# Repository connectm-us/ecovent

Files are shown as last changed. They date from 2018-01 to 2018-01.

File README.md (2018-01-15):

# ecovent
Open source repository for Ecovent smart vent, hub, and wall sensor designs

## Purpose

To open the hardware to the public, open-source community in an effort to stimulate more effective and cost-efficient designs for hardware.

## Methodology

By leveraging a network of sensors measuring temperature, pressure, humidity in rooms throughout a building, and vents or dampers with temperature and pressure sensors, that can be remotely controlled to provide room by room climate control, we can focus on commoditizing the hardware to open this technology to the mass market.

## Room By Room Climate Control Method

A system including a controlled supply register that has an airflow adjusting mechanism that controls an aperture through which air passes and a register sensor that senses a value of an environmental variable in a systems duct work. The register also includes a communication system and a processor system that controls the airflow adjusting mechanism. The system also includes a sensor platform that senses an environmental variable in a space and transmits and receives information. The system includes a controller that receives information about the environmental variables and a desired set point for the environmental variable in the space, controlled via application. The controller determines a target airflow to achieve the desired set point and transmits information about the target airflow. The register receives information about the target airflow and controls the register adjusting mechanism to achieve the target airflow.

## Mass Market
If we can produce cost-efficient dampers or supply registers and sensors to operate within this system methodology, we can provide a solution to the mass market for less than $500.

## Proven Technology
We have proven this technology over 4 years, with independent studies and in-the-field systems.  We are title 24 compliant as well.  The methodology is proven.  Now we need to commoditize the hardware.

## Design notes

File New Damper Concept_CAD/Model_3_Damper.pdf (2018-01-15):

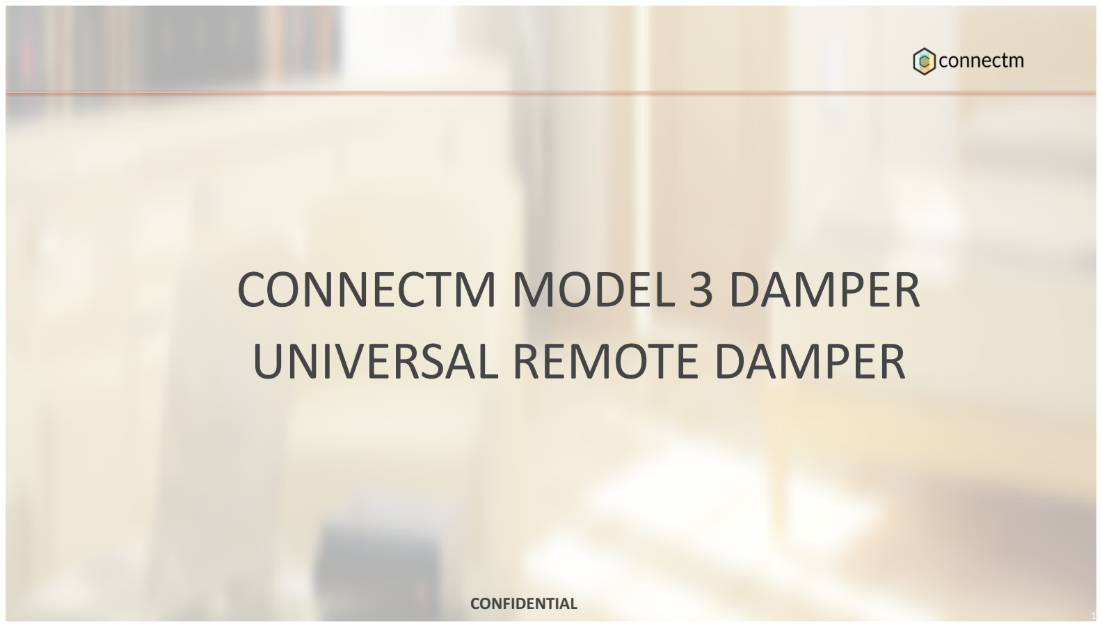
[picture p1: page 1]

# CONNECTM MODEL 3 DAMPER UNIVERSAL REMOTE DAMPER

1

### CONFIDENTIAL

Page 2

# Key Requirements

# - Interface with standard straight vent HVAC boot (4”, 6”, & 8” diameter)

## – Sheet metal construction – 4” diameter vent chosen for layout

# - Target Cost: ~$20 - Target volume: 500k-1M units per year - Operating Environment

## – Temperature: 0-85 C – Humidity: Standard HVAC

# - Target Flow Rate: 0-125 CFM - Target Pressure: 0”-2” H2O - Low Noise - Batteries:

## – 3-5 year life – User-accessible compartment

# - Duty Cycle: 10 full open/close cycles per day - Open / Close Speed: no specific requirement (slow speed OK)

CONFIDENTIAL

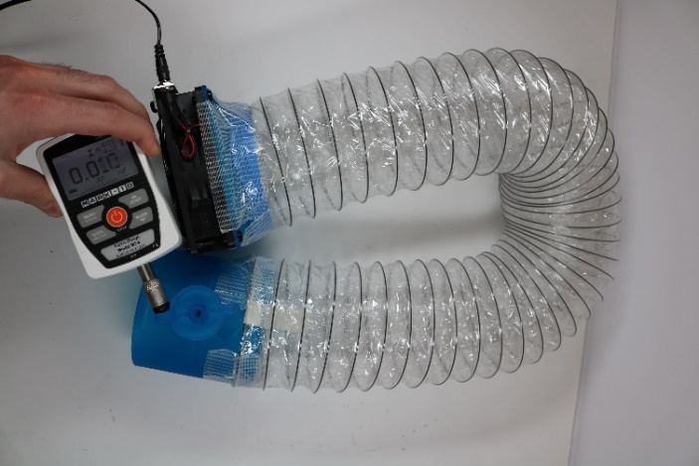
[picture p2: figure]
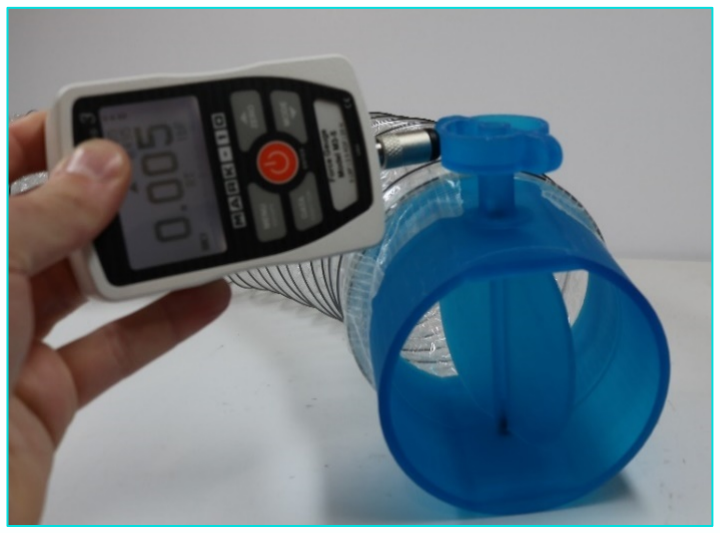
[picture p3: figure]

Page

3

# Motor Torque Requirement Testing

# - Motor sourcing exercise required evaluation of approximate expected open/close damper torque - Off the shelf 120 CFM fan operating at 0.4”

H20 used as airflow source.

# - Rapid prototype damper and housing printed

# - Torque range measured as follows: – Measured peak torque: 0.025 in-lbs (2.8

# mNm

)

# – 5x Safety Factor applied – Target motor torque: 0.120 in -lbs (13 mNm

)

CONFIDENTIAL

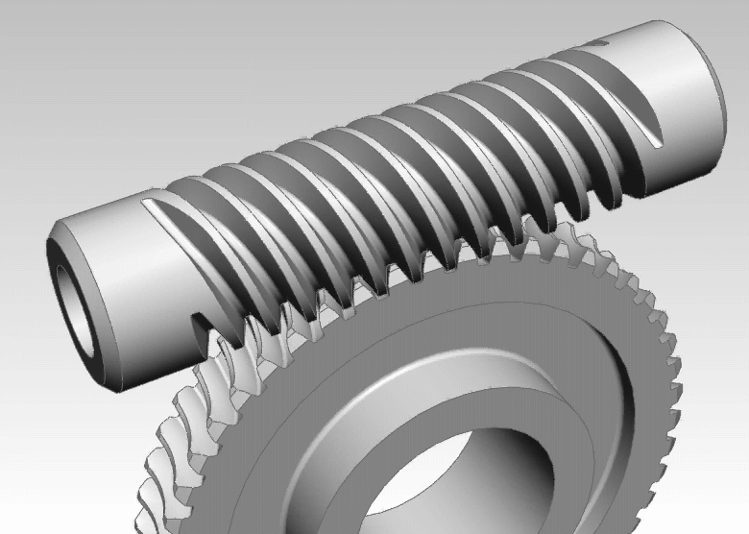
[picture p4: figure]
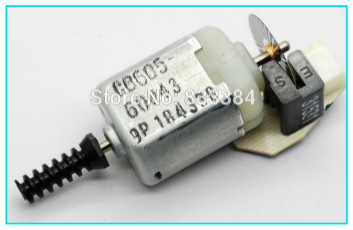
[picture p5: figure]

Page

4

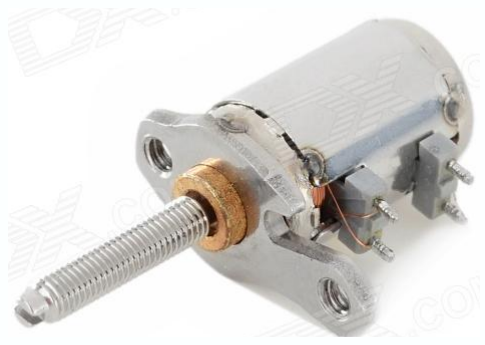
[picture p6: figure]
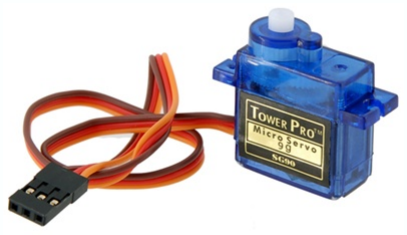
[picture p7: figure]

# 1.Drive Options:

# 1.DC Motor 2.Stepper Motor 3.Servo Motor

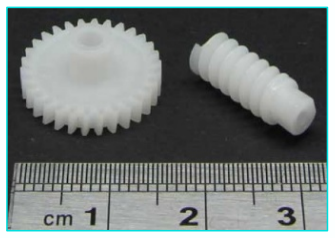
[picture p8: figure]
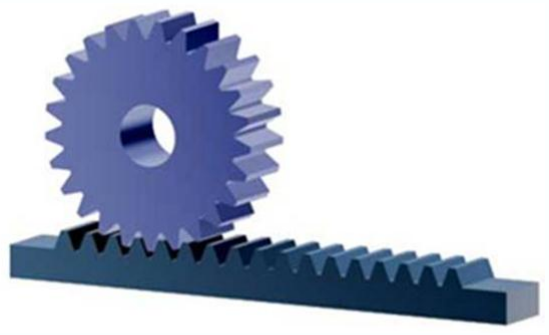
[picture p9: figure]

# 2.Drivetrain Options:

# 1.Worm Gear 2.Rack and Pinion

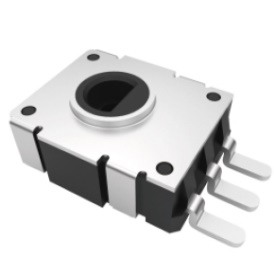
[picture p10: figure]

# 3.Belt Drive

# 3.Rotational Position Sensor

# 1.Stepper with zeroing / calibration 2.Potentiometer with lookup value 3.Encoder direct on motor

# Motor / Drivetrain / Position Options

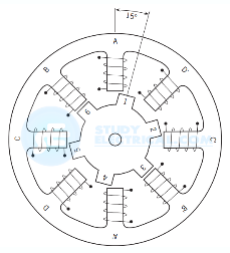
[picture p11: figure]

CONFIDENTIAL

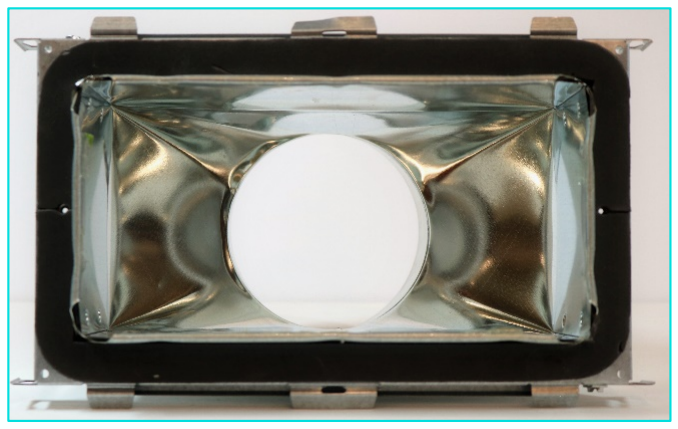
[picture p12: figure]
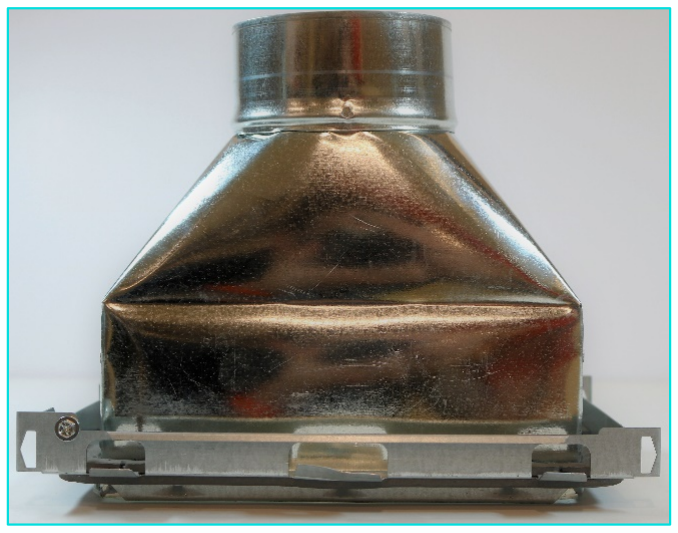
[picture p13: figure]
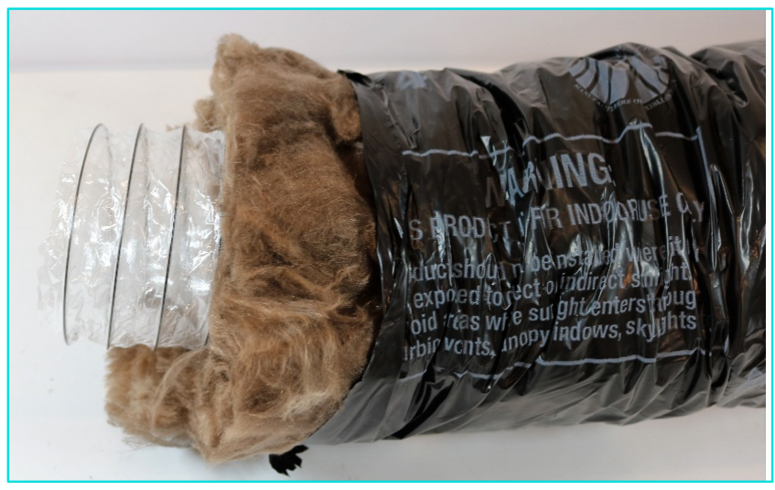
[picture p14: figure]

ConnectM Technology Solutions | Page 5

# HVAC Design Constraints

# - 4” x 8” HVAC straight vent boot - 4” Insulated flexible ducting

# CAD Layout Review

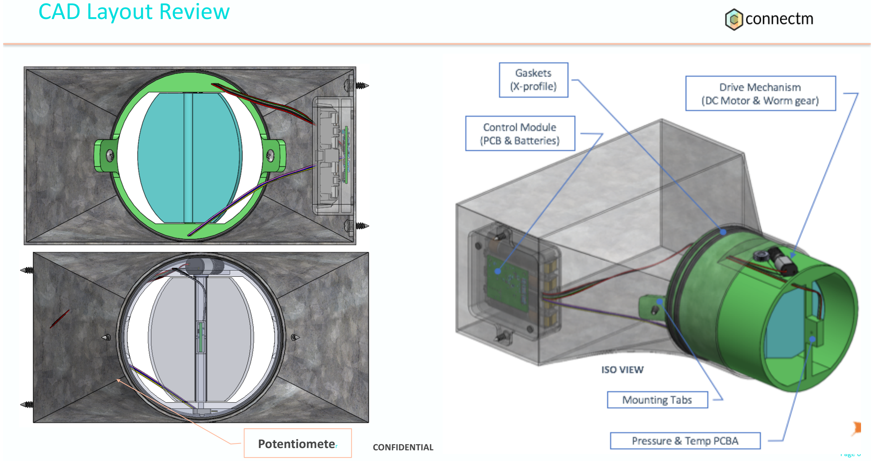
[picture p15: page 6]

CONFIDENTIAL
Page 6

### Potentiometer

Page 7

# Preliminary BOM Estimate

Level | Qty. | Component | Est. Cost (500k/yr) | Ext. Cost | Comments
0 | 1 | CONTROL MODULE ASSY | $ | 6.85 | $ | 6.85
1 | 1 | Control Module Housing, Bottom | $ | 1.00 | $ | 1.00 Estimated for plastic injection molding
1 | 1 | Control Module Housing, Cover | $ | 0.40 | $ | 0.40 | Estimated for plastic injection molding
1 | 2 | Closure Magnets | $ | 0.05 | $ | 0.10 Approximate Pricing from K&J Magnetics
1 | 2 | Double (-) AA Clip Contact | $ | 0.20 | $ | 0.40 | Approximate Pricing from Digi-Key (MPD Devices part)
1 | 2 | Double (+) AA Clip Contact | $ | 0.20 | $ | 0.40 Approximate Pricing from Digi-Key (MPD Devices part)
1 | 1 | PCB Control Assemby | $ | 5.00 | $ | 5.00 | Ecovent to confirm cost
1 | 4 | AA Battery | $ | 0.10 | $ | 0.40 Approximate Pricing from Digi-Key
0 | 1 | DAMPER ASSY | $ | 8.95 | $ | 9.30
1 | 1 | Pressure & Temp PCBA | $ | 3.00 | $ | 3.00 Ecovent to confirm cost
1 | 1 | Damper Housing | $ | 2.00 | $ | 2.00 | Estimated for plastic injection molding
1 | 1 | Damper Valve | $ | 0.50 | $ | 0.50 Estimated for plastic injection molding
1 | 1 | Worm Gear | $ | 0.25 | $ | 0.25 | Estimated for plastic injection molding
1 | 1 | Worm Drive | $ | 0.35 | $ | 0.35 Estimated for plastic injection molding
1 | 2 | O-Ring | $ | 0.35 | $ | 0.70 | Estimate for LSR injection molding
1 | 1 | DC Motor | $ | 2.50 | $ | 2.50 Based on discussions with Mabuchi and Nidec
1 | 1 | Potentiometer | $ | 0.10 | $ | 0.10 | Based on discussions with Polyshine
0 | 1 | MOTOR WIRE HARNESS | $ | 0.25 | $ | 0.25 Estimate
0 | 1 | MEASUREMENT WIRE HARNESS | $ | 0.50 | $ | 0.50 | Estimate
0 | 1 | POT WIRE HARNESS | $ | 0.25 | $ | 0.25 Estimate
0 | 1 | MANUAL ASSEMBLY | $ | 2.50 | $ | 2.50 | 10 min assy time estimate @ $15/hr
| | TOTAL BOM COST: | | | $ | 19.65
| | | | CONFIDENTIAL

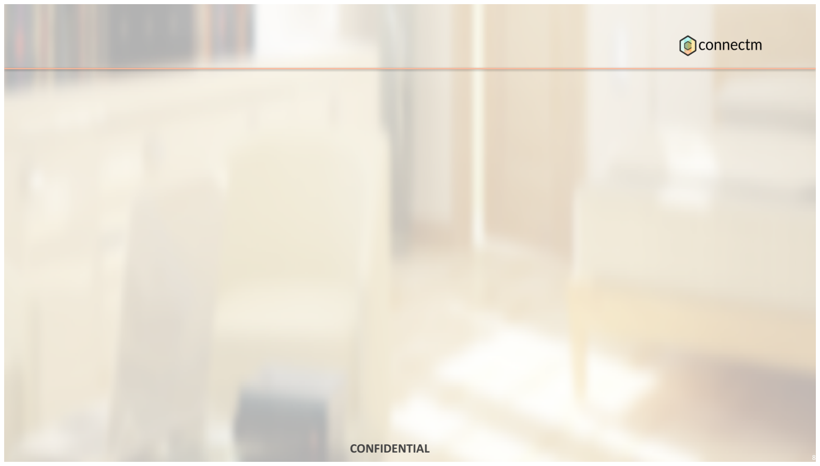
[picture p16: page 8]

8

### CONFIDENTIAL

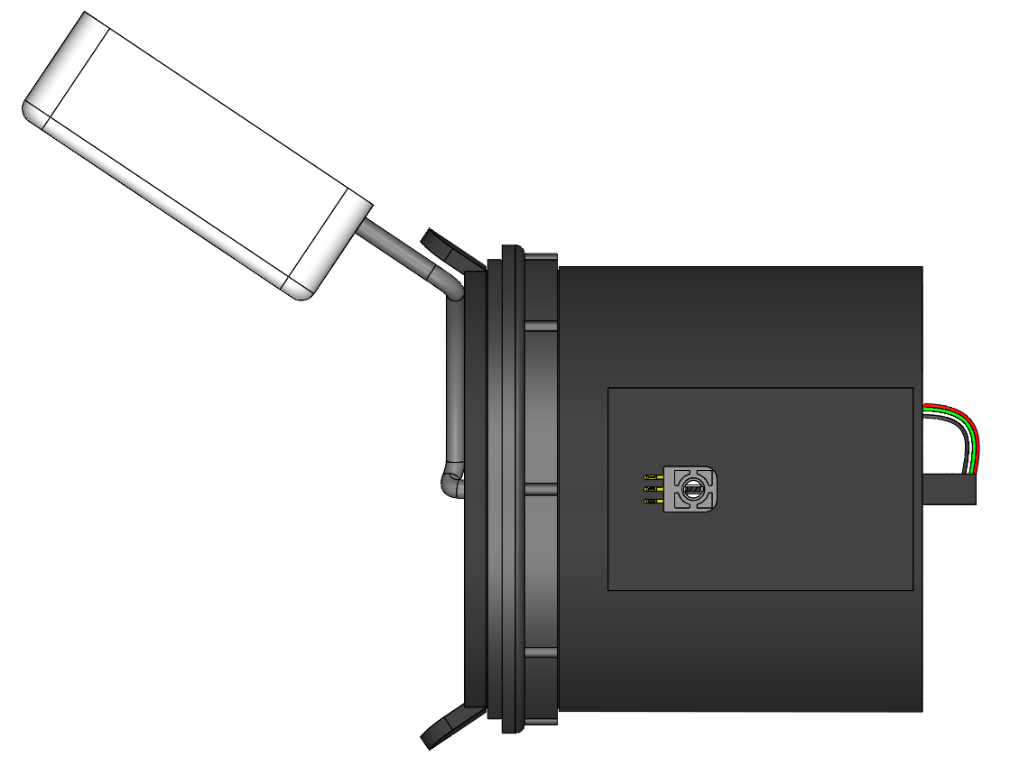
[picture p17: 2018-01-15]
New Damper Concept_CAD/Bottom.png

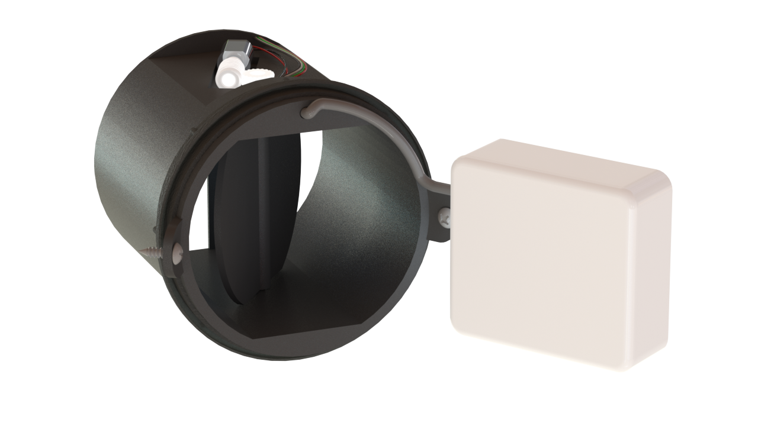
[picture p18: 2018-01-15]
New Damper Concept_CAD/Ecovent From Perspective 2.png

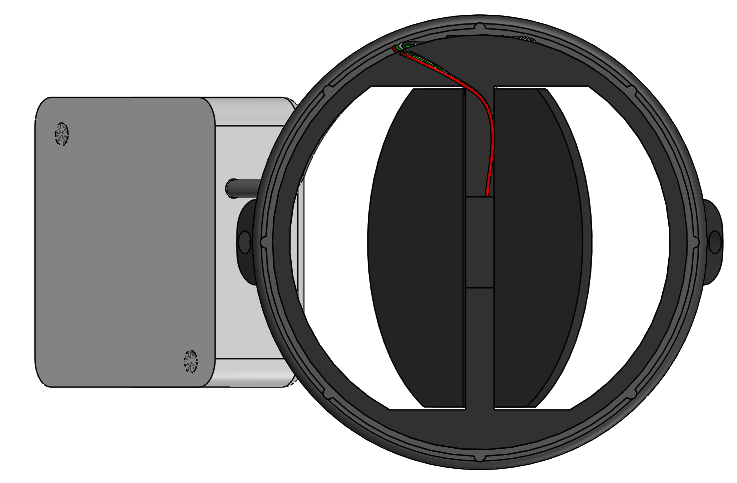
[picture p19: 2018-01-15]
New Damper Concept_CAD/Back.png

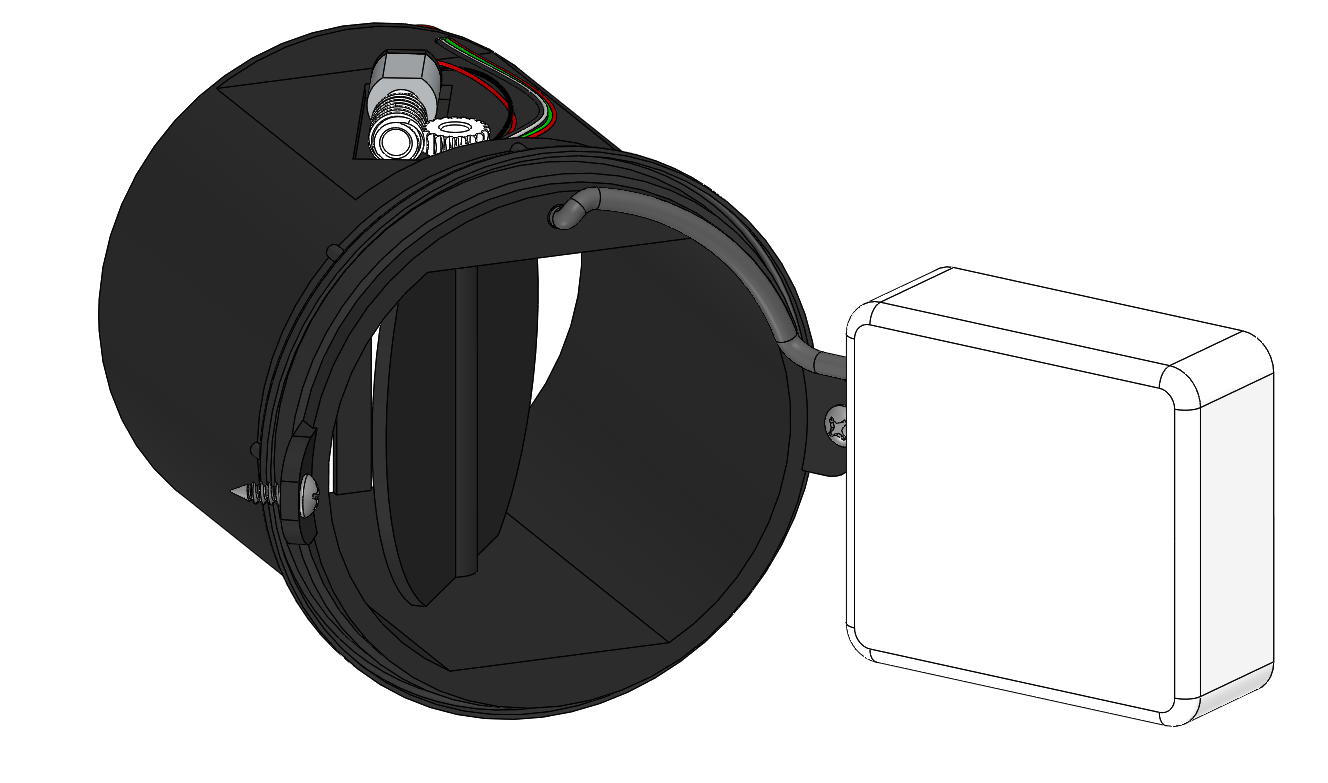
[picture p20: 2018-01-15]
New Damper Concept_CAD/Ecovent Front Perspective 1.png

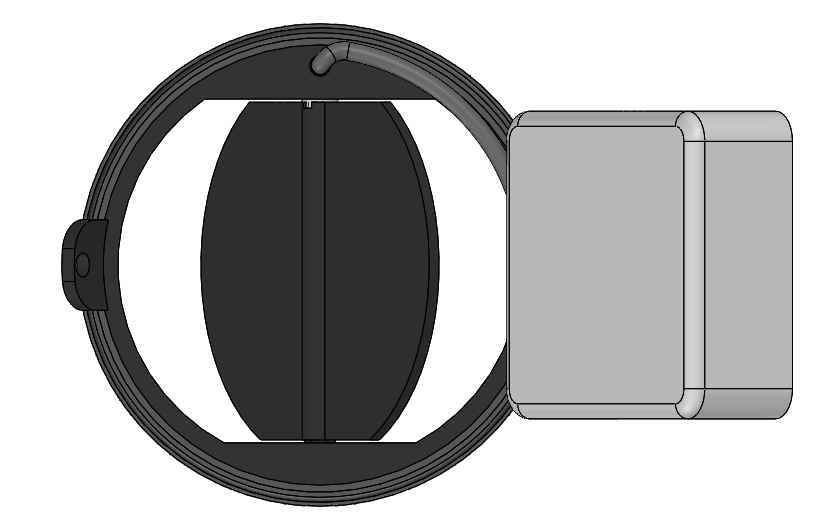
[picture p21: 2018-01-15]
New Damper Concept_CAD/Front.png

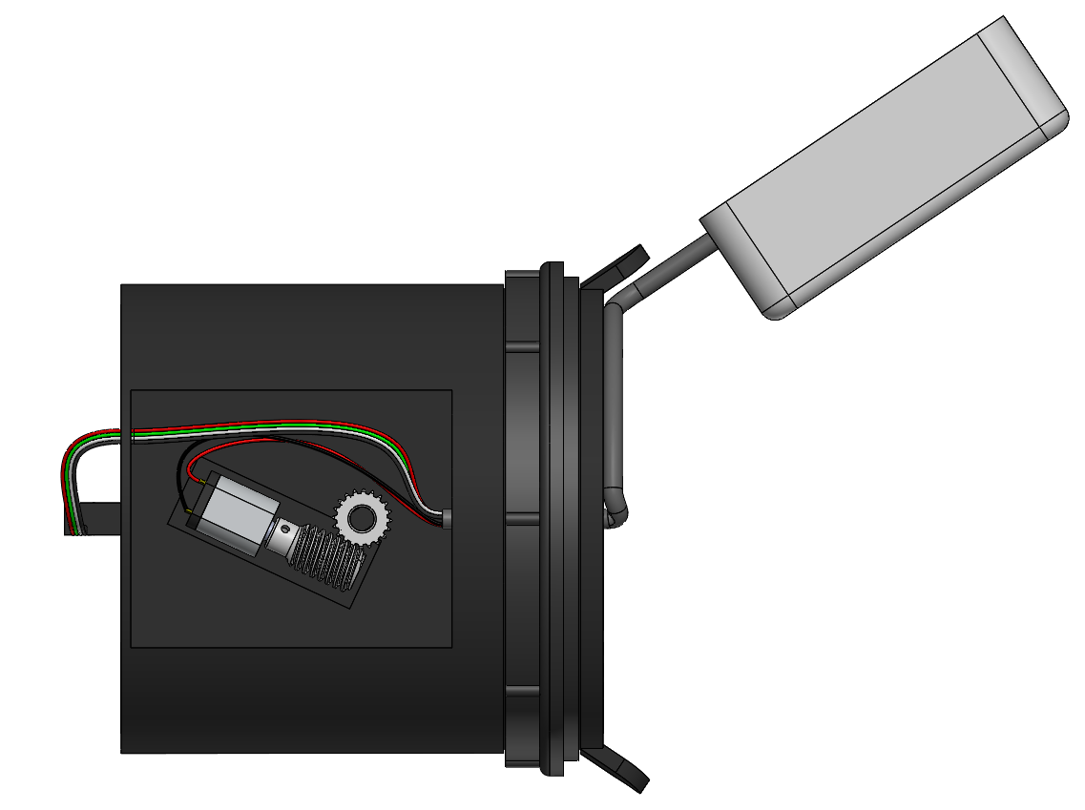
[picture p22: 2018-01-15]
New Damper Concept_CAD/Top.png

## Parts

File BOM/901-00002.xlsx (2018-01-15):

level | item_number | item_name | revision | description | quantity | reference_designator | bom_notes | manufacturer_item_name_2
0 | 901-00002 | Vent 10x6 Wall | J | Wall Vent 10x6
1 | 000-00016 | Label Contents, Vent 10x6 Wall Pulp | A | Label Contents, Vent 10x6 Wall Pulp packaging | 1 |  | Pulp Packaging Label Contents
1 | 000-00026 | Label Contents, FCC, IC, and ETL Vent | A | Label Contents, FCC, IC, and ETL Vent | 2 |  | Device Label Contents
1 | 102-00067 | Battery AA Alkaline | C | Battery AA, common size, all locations | 4 | A
1 | 201-00002 | Vent 10x6 Wall | B | Vent 10x6 Wall | 1
1 | 403-00006 | Physical Label, 1x2 | A | Physical Label Material: The polyester label and acrylic permanent adhesive Size: 1x2 Color: White Thermal transfer printable glossy white polyester label stock; pressure-sensitive permanent "Type P", secured by adhesive and approved UL 969 for indoor use, suitable for use on FRPA100X ABS/PC plastic. -40 C to +100 C ETL controlled part | 3 | B
1 | 403-00008 | Red Arrow Label | A | Label, White, Blank, Width 0.65 in, Height 0.20 in, Polyester, Labels per roll: 10,000, 4 labels wide. Brady R4402-RD 984' Length x 3.27" Width, 4400 Series Red Thermal Transfer Printer Ribbon | 3 | C
1 | 603-00011 | Screw #8x2" Drywall/Sheet Metal | A | screw for drywall into sheet metal, philips | 2 | D
1 | 603-00016 | Washer #8 metal bonded sealing | A | Washer #8 metal bonded sealing | 2 | E
1 | 701-00001 | Vent PCA | G | Vent PCA | 1 | G
2 | 101-00001 | Antenna Mitsubishi | A | Mitsubishi SMD Chip Antenna 3.0X10.5mm | 1 | A1
2 | 101-00005 | 0.1uF 16V 1005 (0402) | A | Capacitor Ceramic 0.1uF 16V X7R 10% 1005 (0402) | 20 | C1, C2, C3, C4, C7, C15, C16, C21, C27, C29, C32, C35, C44, C47, C48, C49, C54, C55, C57, C58
2 | 101-00006 | 1uF 10V 1005 (0402) | A | Capacitor Ceramic 1uF 10V X5R 10% 1005 (0402) | 4 | C9, C34, C43, C45
2 | 101-00007 | 10uF 10V 1608 (0603) | A | Capacitor Ceramic 10uF 10V X5R 20% 1608 (0603) | 6 | C5, C6, C19, C30, C56, C59
2 | 101-00008 | 10nF 10V 1005 (0402) | A | Capacitor Ceramic 10nF 10V X7R 10% 0402 (1005) | 2 | C8, C42
2 | 101-00010 | 27pF 50V 1005 (0402) | A | Capacitor Ceramic 27pF 50V NP0 5% 1005 (0402) | 2 | C12, C13
2 | 101-00011 | 10uF 10V 2012 (0805) | A | Capacitor Ceramic 10uF 10V X5R 10% 2012 (0805) | 6 | C20, C22, C23, C24, C25, C26
2 | 101-00012 | 4.7uF 10V 2012 (0805) | A | Capacitor Ceramic 4.7uF 10V X5R 10% 2012 (0805) | 1 | C14
2 | 101-00013 | 100pF 16V 0402 (1005) | A | Capacitor Ceramic 100pF 16V C0G 10% 0402 (1005) | 3 | C28, C31, C33
2 | 101-00014 | 330pF 50V 1005 (0402) | A | Capacitor Ceramic 330pF 50V C0G 5% 1005 (0402) | 5 | C36, C50, C51, C52, C53
2 | 101-00016 | 220pF 50V 1005 (0402) | A | Capacitor Ceramic 220pF 50V C0G 5%1005 (0402) | 2 | C38, C46
2 | 101-00048 | 30pF 50V 0402 | A | Capacitor Ceramic 30pF 50V 5% NP0 0402 | 2 | C37, C39
2 | 101-00050 | 7pF 50V 1005 (0402) | A | Capacitor Ceramic 7pF 50V COG 0.5pF 1005 (0402)` | 2 | C10, C11
2 | 101-00055 | 22nF 50V 1005 (0402) | A | Capacitor Ceramic 22nF 50V X7R 10% 0402 (1005) | 1 | C17
2 | 101-00056 | 10uF 16V 0805 tantalum | A | Capacitor Tantalum 10uF 16V 20% 0805 | 2 | C60, C61
2 | 101-00057 | 0.47uF (470nF) 16V 0402 | A | Capacitor Ceramic 0.47uF (470nF) 16V 10% 0402 | 1 | C18
2 | 101-00059 | Ferrite Bead 220 Ohm | A | FERRITE BEAD 220 Ohm 800mA 0402 | 2 | L1, L8
2 | 101-00063 | 2.2uH 510mA 1007 | A | Inductor 2.2uH 510mA 20% 1007 | 1 | L2
2 | 101-00065 | 2.2uH 1250mA 3.0X3.0mm | A | Inductor 2.2uH 1250mA 20% 3.0X3.0mm | 1 | L3
2 | 101-00066 | 10uH 100mA 0805 | A | Inductor 10uH 100mA 20% 0805 SMD | 1 | L4
2 | 101-00067 | 27nH 300mA 0402 | A | Inductor 27nH 300mA 5% 0402 SMD | 1 | L5
2 | 101-00068 | 100nH 150mA 0402 | A | Inductor 100nH 150mA 5% 0402 SMD | 1 | L6
2 | 101-00070 | 8.7nH 650mA 0603 | A | Inductor 8.7nH 650mA 0.5nH 0603 SMD Wirewound | 1 | L12
2 | 101-00072 | 39nH 400mA 0603 | A | Inductor 39nH 400mA 2% 0603 SMD Wirewound | 1 | L11
2 | 101-00074 | 7.5nH 750mA 0603 | A | Inductor 7.5nH 750mA 0.5nH 0603 SMD Wirewound | 1 | L13
2 | 101-00082 | 100 kOhm 1/16W | A | Resistor 100 kOhm 1/16W 1% 1005 (0402) | 17 | R1, R2, R3, R4, R5, R9, R11, R13, R16, R19, R24, R26, R29, R30, R31, R32, R33
2 | 101-00084 | 0 Ohm 1/16W | A | Resistor 0 Ohm 1/16W 0402 (1005) | 3 | R15, R22, R25
2 | 101-00087 | 100 Ohm 1/16W | A | Resistor 100 Ohm 1/16W 1% 0402 (1005) | 2 | R50, R54
2 | 101-00092 | 0 Ohm 1/10W | A | Resistor 0 Ohm 1/10W 1608 (0603) | 2 | R20, R40
2 | 101-00097 | 10 kOhm 1/16W | A | Resistor 10 kOhm 1/16W 1% 1005 (0402) | 1 | R51
2 | 101-00109 | 49.9 Ohm 1/10W | A | Resistor 49.9 Ohm 1/10W 1% 0402 SMD | 1 | R39
2 | 101-00128 | 22 Ohm 1/10W | A | Resistor 22 Ohm 1/10W 1% 0402 SMD | 11 | R27, R34, R35, R36, R41, R42, R43, R44, R47, R48, R49
2 | 101-00129 | 10 Ohm 1/16W | A | Resistor 10 Ohm 1/16W 1% 0402 (1005) | 1 | R6
2 | 101-00130 | 22 kOhm 1/16W | A | Resistor 22 kOhm 1/16W 1% 0402 (1005) | 1 | R12
2 | 102-00011 | MOSFET P-channel | A | P-MOSFET Single 20V 0.83A Low Vgs | 2 | Q2, Q3
2 | 102-00014 | MCU STM32 48LFQP | A | 48-Pin, Access line, ultra-low-power, 32-bit, 64 kB flash, 32MHz | 1 | U1
2 | 102-00015 | SPIRIT1 RF Transceiver | A | QFN20, Low data rate, low power, sub-1GHZ transceiver | 1 | U2
2 | 102-00016 | LED Green 0603 | A | LED Green(570nm) 0603 | 1 | D1
2 | 102-00017 | Regulator Buck Adj 300mA | A | 360nA Iq Step Down Converter for Low Power Applications, 12WSON | 1 | U4
2 | 102-00018 | Regulator Boost Sync Adj 1A | A | 100nA Iq Step Up Converter for Low Power Applications, 10TDFN | 1 | U5
2 | 102-00019 | Balun Transformer | A | 50 Ohm Balun to Spirit1 With Integrated Harmonic Filter | 1 | U6
2 | 102-00020 | Crystal 32.768kHz 3.2 x 1.5 x 0.9 mm | A | Crystal 32.768kHz 12.5pF 3.2mm x 1.5 mm SMD 3.2 x 1.5 x 0.9 mm | 1 | Y1
2 | 102-00024 | Crystal 50MHz | A | Crystal Oscillator 50.000MHz 18pF 3.2mm x 2.5mm x 0.9mm | 1 | Y3
2 | 102-00052 | Crystal 16MHz | A | Crystal 16MHz 5.0X3.2mm | 1 | Y2
2 | 102-00063 | IC VOLT-LEVEL TRANSLATOR 12UQFN | A | 4-bit Bidirectional Voltage Translator | 2 | U9, U10
2 | 102-00064 | SPI Flash 8Mbit | B | SPI Flash 8Mbit | 1 | U7
2 | 102-00065 | Trinamic driver for two-phase bipolar stepper motor | A | Universal high voltage controller/driver for two-phase bipolar stepper motor | 1 | U3
2 | 103-00016 | Molex Connector Male socket 4 position | A | Molex Connector Male socket 4 position Pico-EZMate series Mating view: Height: 1.55 mm Width: 4.5 mm Length: 6.6 mm | 2 | P2, P4
2 | 103-00018 | Molex Connector Male socket 2 position | A | Molex Connector Male socket 2 position Pico-EZMate series Mating view: Height: 1.55 mm Width: 4.5 mm Length: 4.2 mm | 1 | P3
2 | 103-00027 | Switch SPST | A | Push Button 0.05A 32V SPST-NO 4.6X2.8mm | 1 | PB1
2 | 201-00028 | Vent PCB Assembly Drawing | A |  | 1
2 | 301-00001 | Vent PCB | E | Vent PCB | 1 | PCB1
2 | 520-00006v1.0.8 | Vent Firmware | A |  | 1 |  | Vent firmware to be programmed on vent PCBA
1 | 701-00009 | Pressure Sensor PCA | D | Pressure Sensor PCA (pressure and temperature) NO CLEAN | 1 | H
2 | 101-00005 | 0.1uF 16V 1005 (0402) | A | Capacitor Ceramic 0.1uF 16V X7R 10% 1005 (0402) | 1 | C1
2 | 101-00007 | 10uF 10V 1608 (0603) | A | Capacitor Ceramic 10uF 10V X5R 20% 1608 (0603) | 2 | C2, C3
2 | 101-00097 | 10 kOhm 1/16W | A | Resistor 10 kOhm 1/16W 1% 1005 (0402) | 2 | R1, R3
2 | 101-00128 | 22 Ohm 1/10W | A | Resistor 22 Ohm 1/10W 1% 0402 SMD | 1 | R6
2 | 102-00056 | MEMS Pressure Sensor | A | IC MEMS Pressure Sensor 10HCLGA | 1 | U1
2 | 103-00016 | Molex Connector Male socket 4 position | A | Molex Connector Male socket 4 position Pico-EZMate series Mating view: Height: 1.55 mm Width: 4.5 mm Length: 6.6 mm | 1 | P1
2 | 301-00004 | Pressure Sensor PCB | D | Pressure Sensor PCB | 1 | PCB1
1 | 701-00015 | Battery Connector PCA | C | Ecovent battery connector PCA | 1 | I
2 | 103-00018 | Molex Connector Male socket 2 position | A | Molex Connector Male socket 2 position Pico-EZMate series Mating view: Height: 1.55 mm Width: 4.5 mm Length: 4.2 mm | 1 | P2
2 | 301-00012 | Battery Connector PCB | C | Battery Connector PCB | 1
1 | 801-00033 | Cable, Vent Battery Power, 3 in Wire, 2 position Molex on 2 sides | F | Molex Connectors on both ends of the wires Molex Connectors are female socket type and each have 2 positions Wire length is 3" +/-0.25" | 1 | J
2 | 101-00023 | Wire 28 awg, 3 in, UL rated | D | Wire 28 awg, 7/36 stranded Insulation: 0.0055" PTFE Overall diameter: 0.028" Length 3" +/- 0.25" UL rated RoHS compliant | 2
2 | 103-00014 | Molex Crimp for 28-30 AWG wire | A | Molex Crimp for 28-30 AWG wire Goes in the molex connector Pico-EZMate series | 4
2 | 103-00019 | Molex Connector Female socket 2 position | A | Molex Connector Female socket 2 position Pico-EZMate series Mating view: Height: 1.3 mm Width: 2.6 mm Length: 3.5 mm | 2
2 | 201-00063 | Cable, Vent Battery Power, 3 in Wire, 2 position Molex on 2 sides | B | Cable, Vent Battery Power, 3 in Wire, 2 position Molex on 2 sides | 1
1 | 900-00002 | Vent 10x6 Wall Ordering Code NSM | G | Vent 10x6 Wall Ordering Code NSM | 1 | F
2 | 201-00019 | Vent 10x6 Wall Ordering Code NSM | B | Vent 10x6 Wall Ordering Code NSM | 1
2 | 401-00079 | Vent 10x6 Wall Pulp Pack | B | Packaging Assembly - pulp packaging clamshell with rubber bands - holds 1 10x6 wall vent | 1 |  | Packaging for vent
3 | 401-00031 | Vent 10x6 Bottom Pulp Molded | A | Packaging - holds 1 10x6 wall/ceiling/floor vent - bottom half of pulp molded assembly | 1
3 | 401-00032 | Vent 10x6 Top Pulp Molded | A | Packaging - holds 1 10x6 wall/ceiling/floor vent - top half of pulp molded assembly | 1
3 | 401-00052 | Vent 10x6 Wall Foam Insert | A | Packaging - Foam Insert - insert into 10x6 wall vent pulp molded packaging assembly | 1
3 | 401-00055 | Battery Pack Foam Insert | A | Packaging - Foam Insert - Battery Pack | 1
3 | 401-00072 | Rubber Band 8 Inch | A | Packaging - Rubber Band 8" length, .05" thick, .38" wide - used to hold pulp packaging together | 2
3 | 401-00088 | Vent Packaging Poly Bag | A | Plastic bag for packaging vents prior to pulp packaging. | 1
2 | 602-00076 | Balljoint Faceplate Wall/Ceiling | E | Vent Deflector, common size, wall and ceiling vents | 1 | A
2 | 602-00078 | Vent PCB Cover | G | Vent PCB Cover, common size, multiple locations | 1 | B
2 | 602-00082 | Vent Pressure Sensor Cover 10 inch | D | Vent Pressure Sensor Cover 10" inch, multiple locations. White for wall and ceiling vents. Black for floor vents. | 1 | C
2 | 603-00019 | Screw M2.5x6 Flat Head Plastite | B | Screw M2.5x6 Flat Head Plastite | 4 |  | These screws are to be bulk packaged separately with all other screws of this type in the order.
2 | 603-00019 | Screw M2.5x6 Flat Head Plastite | B | Screw M2.5x6 Flat Head Plastite | 8 | D
2 | 604-00005 | Strapping Tape | A | Scotch Film Strapping Tape 8898 (or Ecovent approved equivalent) Width - 18mm Thick - 0.12mm | 1
2 | 801-00008 | Frame 10x6 Wall/Ceiling | D | Wall/Ceiling Vent frame 10x6 with magnets installed. | 1 | E
3 | 201-00038 | Frame Wall/Ceiling | B | Frame Wall/Ceiling assembly drawing for all sizes | 1
3 | 602-00084 | Frame 10x6 Wall/Ceiling | E | Wall/Ceiling Vent Frame 10x6 plastic part | 1 | A
3 | 603-00006 | Magnet 3/8x1/8x1/16 | A | Magnet 3/8x1/8x1/16 used in multiple locations | 4 | B
3 | 604-00009 | Cyanoacrylate Loctite 411 | A | Cyanoacrylate Loctite 411 | 1
2 | 801-00009 | Faceplate Extension 10x6 Wall | D | 10x6 Wall Faceplate Extension | 1 | F
3 | 201-00039 | Faceplate Extension Wall/Ceiling | B | Faceplate Extension Wall/Ceiling assembly drawings for all wall/ceiling vents. | 1
3 | 602-00139 | Faceplate Extension 10x6 Wall | F | Faceplate Extension 10x6 Wall | 1 | A
3 | 603-00006 | Magnet 3/8x1/8x1/16 | A | Magnet 3/8x1/8x1/16 used in multiple locations | 4 | B
3 | 604-00009 | Cyanoacrylate Loctite 411 | A | Cyanoacrylate Loctite 411 | 1
2 | 801-00020 | Battery Pack | E | Vent Battery Pack, common size, all locations | 1 | G
3 | 201-00050 | Battery Pack | B | Battery Pack | 1
3 | 601-00007 | Battery Series Connection | B | Battery Series Connection, Vent | 2 | C
3 | 601-00010 | Battery Spring Negative | B | Battery Spring Negative, Vent | 2 | E
3 | 601-00014 | Battery Pack Terminal | C | Battery Pack Terminal | 4 | D
3 | 601-00016 | Battery Contact Positive | B | Battery Contact Positive, Vent | 2 | F
3 | 602-00060 | Battery Pack Housing | G | Battery Pack Housing; White color for floor and ceiling vents, Brown color for floor vents | 1 | A
3 | 602-00144 | Battery Pack Rib | A | Ribs that attach to the battery pack. White for wall and ceiling vents, Brown for floor vents. | 2 | B
2 | 801-00031 | Main Body 10x6 Wall/Ceiling | E | Vent Main Body 10x6 for wall/ceiling | 1 | H
3 | 201-00051 | Main Body Wall/Ceiling | B | Main Body Wall/Ceiling Assembly Drawing | 1
3 | 602-00081 | Outer Box 10x6 | K | Outer Vent Box, 10x6, all locations. White for wall and ceiling vents. Black for floor vents. | 1 | A
3 | 602-00088 | Flexible Door 10x6 | E | Flexible vent door 10x6. white for wall and ceiling vents. Black for floor vents. | 2 | E
4 | 602-00126 | Door Rib 6 inch | C | Vent Door Rib 6 inch. white for wall and ceiling vents. black for floor vents. | 2
4 | 602-00145 | Door Rib 6 inch, no snap | B | Door Rib 6 inch, no snap. white for wall and ceiling vents. black for floor vents. | 7
3 | 602-00089 | Vent Seal 10x6 wall/ceiling, white | B | Vent Seal 10x6 wall/ceiling, white | 1 | B
3 | 603-00006 | Magnet 3/8x1/8x1/16 | A | Magnet 3/8x1/8x1/16 used in multiple locations | 4 | C
3 | 604-00009 | Cyanoacrylate Loctite 411 | A | Cyanoacrylate Loctite 411 | 1
2 | 801-00032 | Drivetrain Insert 10x6 Wall/Ceiling | G | Vent Drivetrain Insert 10x6, Wall and Ceiling | 1 | I
3 | 103-00045 | Motor Stepper 25mm with 200mm wires and Molex connector | A | Vent Drivetrain, 25mm bipolar, ungeared stepper motor with 200mm wires and Female Molex connector on the other end of wires, all locations. | 1 | H
3 | 201-00052 | Drivetrain Insert Wall/Ceiling | B | Drivetrain Insert Wall/Ceiling Assembly Drawing | 1
3 | 602-00053 | Lead Screw 10 inch | C | Vent Drivetrain, Lead Screw, 10 inch, all locations. | 1 | D
3 | 602-00055 | Bushing | F | Bushing for screw | 1 | G
3 | 602-00073 | Nut, Bushing Side | F | Nut, Bushing Side | 1 | E
3 | 602-00083 | Diffuser Screw Cover 10x6 | F | Diffuser Screw Cover 10x6. White for wall and ceiling vents. Black for floor vents. | 1 | A
3 | 602-00085 | Nut, Motor Side | F | Nut, Motor Side | 1 | F
3 | 602-00086 | Motor Cover Front | A | Front Rubber Cover for Motor | 1 | B
3 | 603-00004 | Washer M3 rubber | A | Washer M3 rubber | 6 | I
3 | 603-00005 | Screw M3x8 Plastite | A | Plastite Screw, M3x8 | 4 | J
3 | 603-00014 | Screw M2x10 BH Machine | A | Vent drivetrain, m2x10 bh machine screw, all locations. | 1 | K
3 | 603-00018 | Locknut M2 Hex Stainless Steel | A | Nylon Insert Locknut M2x0.4 Hex Stainless Steel | 1 | L
3 | 801-00053 | Cable, Vent Pressure Sensor, 16 in Wire, 4 position Molex on 2 sides | F | Molex Connectors on both ends of the wires Molex Connectors are female socket type and each have 4 positions Wire length is 16" +/- 0.25" | 1 | M
4 | 101-00032 | Wire 28 awg, 16 in, UL rated | D | Wire 28 awg, 7/36 stranded Insulation: 0.0055 PTFE Overall diameter: 0.028 Length 16" +/- 0.25" UL rated RoHS Compliant | 4 | C
4 | 103-00014 | Molex Crimp for 28-30 AWG wire | A | Molex Crimp for 28-30 AWG wire Goes in the molex connector Pico-EZMate series | 8 | B
4 | 103-00017 | Molex Connector Female socket 4 position | A | Molex Connector Female socket 4 position Pico-EZMate series Mating view Height: 1.3 mm Width: 5 mm Length: 3.5 mm | 2 | A
4 | 201-00083 | Cable, Vent Pressure Sensor, 16 in Wire, 4 position Molex on 2 sides | B | Cable, Vent Pressure Sensor, 16 in Wire, 4 position Molex on 2 sides | 1
2 | 801-00063 | Faceplate Cover 10x6 Wall | D | Vent, Faceplate Cover, 10x6, Wall | 1 | J
3 | 201-00041 | Faceplate Cover Wall/Ceiling | B | Faceplate Cover Wall/Ceiling Assembly Drawing | 1
3 | 601-00017 | Rectangular Block 3/8 x 1/8 x 1/16, steel | A | Rectangular Block 3/8 x 1/8 x 1/16, steel | 4 | B
3 | 602-00016 | Faceplate Cover 10x6 Wall | G | Vent, Deflector Cover, 10x6, Wall | 1 | A
3 | 604-00009 | Cyanoacrylate Loctite 411 | A | Cyanoacrylate Loctite 411 | 1

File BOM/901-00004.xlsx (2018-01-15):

level | item_number | item_name | revision | description | quantity | reference_designator | bom_notes
0 | 901-00004 | Control Hub |  | Control Hub
1 | 000-00011 | Label Contents, Control Hub Pulp | A | Label Contents, control hub pulp packaging | 1 |  | Packaging Label Contents
1 | 000-00027 | Label Contents, FCC, IC, and ETL Hub | A | Label Contents, FCC, IC, and ETL Hub | 1 |  | Device Label Contents
1 | 201-00004 | Control Hub | C | Control Hub | 1
1 | 403-00006 | Physical Label, 1x2 | A | Physical Label Material: The polyester label and acrylic permanent adhesive Size: 1x2 Color: White Thermal transfer printable glossy white polyester label stock; pressure-sensitive permanent "Type P", secured by adhesive and approved UL 969 for indoor use, suitable for use on FRPA100X ABS/PC plastic. -40 C to +100 C ETL controlled part | 2 | C | Physical Labels
1 | 602-00151 | Cover, Ethernet Plug | A | Cover, Ethernet Plug | 1 |  | Shipped With Unit
1 | 701-00011 | Control Module PCA | F | Ecovent control module PCA. | 1 | B
2 | 000-00004 | DNP - C, L, R | A | Do Not Populate - C203, C201, L31, R15, R82, R105, R203, R204, R205, R206, R207, R208, R19, R20, R100, R104, R202, R25, R92, R97, R163, R165, R166, R167, R168, R169, R170, R171, R84 | 25 | C203, C201, L31, R15, R82, R105, R203, R204, R205, R206, R19, R20, R100, R104, R202, R25, R165, R166, R167, R168, R169, R170, R171, R84, R266
2 | 101-00001 | Antenna Mitsubishi | A | Mitsubishi SMD Chip Antenna 3.0X10.5mm | 1 | A1
2 | 101-00004 | ANTENNA 2.4GHZ 5GHZ SMD | A | ANTENNA 2.4GHZ 5GHZ SMD | 1 | ANT2
2 | 101-00005 | 0.1uF 16V 1005 (0402) | A | Capacitor Ceramic 0.1uF 16V X7R 10% 1005 (0402) | 106 | C1, C2, C3, C4, C5, C6, C7, C8, C9, C10, C11, C12, C13, C14, C15, C16, C17, C18, C19, C20, C21, C22, C23, C24, C25, C26, C27, C28, C33, C34, C35, C36, C45, C48, C51, C52, C53, C60, C62, C63, C65, C67, C69, C72, C73, C75, C79, C80, C82, C83, C84, C85, C86, C87, C88, C89, C90, C91, C92, C93, C94, C95, C97, C98, C99, C100, C101, C102, C103, C105, C106, C108, C110, C112, C113, C114, C117, C118, C120, C164, C166, C169, C172, C174, C176, C178, C188, C189, C190, C191, C194, C195, C200, C204, C205, C206, C207, C212, C213, C214, C217, C218, C222, C223, C225, C226
2 | 101-00006 | 1uF 10V 1005 (0402) | A | Capacitor Ceramic 1uF 10V X5R 10% 1005 (0402) | 4 | C177, C185, C193, C163
2 | 101-00007 | 10uF 10V 1608 (0603) | A | Capacitor Ceramic 10uF 10V X5R 20% 1608 (0603) | 14 | C43, C44, C46, C47, C49, C50, C170, C186, C187, C208, C211, C216, C221, C228
2 | 101-00010 | 27pF 50V 1005 (0402) | A | Capacitor Ceramic 27pF 50V NP0 5% 1005 (0402) | 2 | C198, C199
2 | 101-00013 | 100pF 16V 0402 (1005) | A | Capacitor Ceramic 100pF 16V C0G 10% 0402 (1005) | 3 | C171, C173, C175
2 | 101-00014 | 330pF 50V 1005 (0402) | A | Capacitor Ceramic 330pF 50V C0G 5% 1005 (0402) | 1 | C179
2 | 101-00016 | 220pF 50V 1005 (0402) | A | Capacitor Ceramic 220pF 50V C0G 5%1005 (0402) | 2 | C180, C184
2 | 101-00017 | 0.47uF 200V 1812 | A | Capacitor Ceramic 0.47uF 200V X7R 10% 1812 | 3 | C81, C224, C231
2 | 101-00030 | 0.33F 3.3V COIN SMD | A | Capacitor Super 0.33F 3.3V COIN SMD | 1 | C78
2 | 101-00031 | 0.047uF 6.3V 0402 | A | Capacitor Ceramic 0.047uF 6.3V X7R 0402 | 1 | C54
2 | 101-00034 | 1uF 10V 0603 | A | Capacitor Ceramic 1uF 10V 10% X7R 0603 | 3 | C37, C38, C42
2 | 101-00035 | 3.3uF 6.3V 0805 | A | Capacitor Ceramic 3.3uF 6.3V 10% X7R 0805 | 4 | C55, C56, C57, C58
2 | 101-00036 | 4.7uF 10V 0603 | A | Capacitor Ceramic 4.7uF 10V 10% X5R 0603 | 6 | C61, C66, C70, C71, C77, C96
2 | 101-00042 | 8pF 50V 0402 | A | Capacitor Ceramic 8pF 50V NP0 0402 | 1 | C168
2 | 101-00043 | 10pF 50V 0402 | A | Capacitor Ceramic 10pF 50V 1% NP0 0402 | 2 | C115, C167
2 | 101-00045 | 12pF 50V 0402 | A | Capacitor Ceramic 12pF 50V 5% NP0 0402 | 2 | C109, C111
2 | 101-00046 | 20pF 50V 0402 | A | Capacitor Ceramic 20pF 50V 5% NP0 0402 | 2 | C104, C107
2 | 101-00048 | 30pF 50V 0402 | A | Capacitor Ceramic 30pF 50V 5% NP0 0402 | 2 | C182, C183
2 | 101-00049 | 10000pF 50V 0402 | A | Capacitor Ceramic 10000pF 50V 10% X7R 0402 | 10 | 'C29, C30, C31, C32, C59, C64, C68, C74, C76, C192
2 | 101-00050 | 7pF 50V 1005 (0402) | A | Capacitor Ceramic 7pF 50V COG 0.5pF 1005 (0402)` | 2 | C196, C197
2 | 101-00052 | 10uF 25V 0805 | A | Capacitor Ceramic 10uF 25V 10% X5R 0805 | 5 | C116, C119, C165, C219, C227
2 | 101-00053 | 2.2pF 50V 0402 | A | Capacitor Ceramic 2.2pF 50V NPO 0402 | 1 | C202
2 | 101-00054 | 4.7uF 10V 0805 | A | Capacitor Ceramic 4.7uF 10V 10% X7R 0805 | 3 | C39, C40, C41
2 | 101-00059 | Ferrite Bead 220 Ohm | A | FERRITE BEAD 220 Ohm 800mA 0402 | 3 | L8, L11, L35
2 | 101-00060 | FERRITE CHIP 300 Ohm 0603 SMD | A | FERRITE CHIP 2A 300 Ohm 0603 SMD | 13 | L4, L5, L7, L10, L12, L16, L17, L18, L19, L20, L36, L37, L38
2 | 101-00066 | 10uH 100mA 0805 | A | Inductor 10uH 100mA 20% 0805 SMD | 1 | L28
2 | 101-00067 | 27nH 300mA 0402 | A | Inductor 27nH 300mA 5% 0402 SMD | 1 | L29
2 | 101-00068 | 100nH 150mA 0402 | A | Inductor 100nH 150mA 5% 0402 SMD | 1 | L30
2 | 101-00070 | 8.7nH 650mA 0603 | A | Inductor 8.7nH 650mA 0.5nH 0603 SMD Wirewound | 1 | L33
2 | 101-00072 | 39nH 400mA 0603 | A | Inductor 39nH 400mA 2% 0603 SMD Wirewound | 1 | L32
2 | 101-00074 | 7.5nH 750mA 0603 | A | Inductor 7.5nH 750mA 0.5nH 0603 SMD Wirewound | 1 | L34
2 | 101-00078 | 2.2uH 1.8A | A | Inductor 2.2uH 1.8A 80mOhmSMD | 3 | L1, L2, L3
2 | 101-00080 | 10uH 115mA 0603 | A | Inductor 10uH 115mA 10% 0603 | 5 | L6, L9, L13, L14, L15
2 | 101-00081 | 1.1nH 1A 0402 | A | FIXED IND 1.1NH 1A 100 MOHM SMD | 1 | L27
2 | 101-00084 | 0 Ohm 1/16W | A | Resistor 0 Ohm 1/16W 0402 (1005) | 37 | R9, R10, R11, R12, R13, R17, R18, R28, R33, R34, R35, R36, R38, R45, R52, R53, R55, R58, R60, R62, R63, R64, R69, R71, R75, R79, R95, R96, R112, R127, R161, R179, R207, R208, R232, R233, R237
2 | 101-00097 | 10 kOhm 1/16W | A | Resistor 10 kOhm 1/16W 1% 1005 (0402) | 14 | R23, R29, R92, R97, R106, R114, R115, R119, R120, R172, R198, R210, R239, R245
2 | 101-00107 | 0.0 Ohm 1/10W | A | Resistor 0.0 Ohm 1/10W JUMP 0603 SMD | 10 | R39, R40, R41, R44, R48, R76, R77, R78, R80, R235
2 | 101-00108 | 1 Ohm 1/16W | A | Resistor 1 Ohm 1/16W 1% 0402 SMD | 6 | R26, R50, R57, R66, R67, R74
2 | 101-00109 | 49.9 Ohm 1/10W | A | Resistor 49.9 Ohm 1/10W 1% 0402 SMD | 10 | R70, R81, R83, R85, R108, R124, R234, R236, R238, R244
2 | 101-00111 | 200 Ohm 1/10W | A | Resistor 200 Ohm 1/10W 1% 0402 SMD | 1 | R72
2 | 101-00112 | 240 Ohm 1/10W | A | Resistor 240 Ohm 1/10W 1% 0402 SMD | 3 | R1, R2, R21
2 | 101-00113 | 390 Ohm 1/16W | A | Resistor 390 Ohm 5% 1/16W 0402 | 4 | R86, R220, R246, R247
2 | 101-00114 | 470 Ohm 1/16W | A | Resistor 470 Ohm 1/16W 1% 0402 SMD | 8 | R5, R6, R90, R93, R131, R132, R133, R192
2 | 101-00115 | 1 kOhm 1/16W | A | Resistor 1 kOhm 0402 (1005) 1% 1/16W SMD | 9 | R37, R56, R59, R68, R211, R241, R242, R263, R265
2 | 101-00116 | 1.5 kOhm 1/16W | A | Resistor 1.5 kOhm 1/16W 1% 0402 SMD | 6 | R30, R31, R49, R54, R65, R73
2 | 101-00117 | 4.7 kOhm 1/10W | A | Resistor 4.7 kOhm 1/10W 1% 0402 SMD | 15 | R87, R99, R107, R122, R184, R209, R213, R248, R249, R250, R251, R252, R254, R256, R257
2 | 101-00118 | 5.62 kOhm 1/16W | A | Resistor 5.62 kOhm 1/16W 1% 0402 SMD | 1 | R111
2 | 101-00120 | 49.9 kOhm 1/16W | A | Resistor 49.9 kOhm 1/16W 1% 0402 SMD | 2 | R42, R43
2 | 101-00122 | 100 kOhm 1/16W | A | Resistor 100 kOhm 1/16W 1% 0402 SMD | 28 | R14, R16, R22, R24, R27, R32, R46, R47, R51, R61, R88, R89, R98, R101, R102, R103, R109, R135, R162, R163, R180, R181, R182, R185, R191, R199, R200, R201
2 | 101-00125 | 200 kOhm 1/16W | A | Resistor 200 kOhm 1/16W 1% 0402 SMD | 1 | R110
2 | 101-00128 | 22 Ohm 1/10W | A | Resistor 22 Ohm 1/10W 1% 0402 SMD | 21 | R91, R94, R113, R116, R117, R118, R123, R125, R126, R130, R164, R175, R176, R177, R178, R183, R186, R187, R188, R189, R190
2 | 101-00159 | Cap-1005 (0402) CER 18pF 50V C0G 2% | A | Cap-1005 (0402) CER 18pF 50V C0G 2% | 2 | C121, C122
2 | 101-00160 | CAP CER 0.1UF 25V Y5V 0402 | A | CAP CER 0.1UF 25V Y5V 0402 | 1 | C181
2 | 101-00162 | CAP CER 47UF 6.3V 20% X5R 0805 (2012) | A | CAP CER 47UF 6.3V 20% X5R 0805 (2012) | 4 | C209, C210, C215, C220
2 | 101-00164 | 11.8K OHM 1% 1/16W 0402 | A | RES SMD 11.8K OHM 1% 1/16W 0402 | 1 | R240
2 | 101-00168 | 16 Ohm 1% 1/16W 0402 | A | RES SMD 16 OHM 1% 1/16W 0402 | 1 | R3
2 | 101-00169 | 51 Ohm 1% 1/16W 0402 | A | RES SMD 51 OHM 1% 1/16W 0402 | 1 | R4
2 | 101-00170 | 100 Ohm 1% 1/16W 0402 | A | RES SMD 100 OHM 1% 1/16W 0402 | 1 | R7
2 | 102-00004 | DIODE ZENER 5.1V 1W | A | DIODE ZENER 5.1V 1W SOD123 | 1 | D4
2 | 102-00005 | DIODE SWITCHING 75V 0.15A | A | DIODE SWITCHING 75V 0.15A SOD323 | 2 | D13, D14
2 | 102-00006 | DIODE SCHOTTKY 30V 200MA | A | DIODE SCHOTTKY 30V 200MA SOT23 | 1 | U6
2 | 102-00007 | LED RED 0603 | A | LED Red 0603 20mA | 1 | D10
2 | 102-00008 | LED RGB Square SMD | A | Led RGB Square Clear 1.0X1.0mm | 2 | D7, D11
2 | 102-00009 | LED GREEN CLEAR 0603 | A | LED GREEN CLEAR 0603 SMD | 2 | D1, D5
2 | 102-00010 | LED SUPER RED DIFF 0603 | A | LED 660NM SUPER RED DIFF 0603SMD | 2 | D2, D6
2 | 102-00013 | MOSFET N-CH 20V | A | MOSFET N-CH 20V 4.2A SOT-23 | 1 | U5
2 | 102-00014 | MCU STM32 48LFQP | A | 48-Pin, Access line, ultra-low-power, 32-bit, 64 kB flash, 32MHz | 1 | U17
2 | 102-00015 | SPIRIT1 RF Transceiver | A | QFN20, Low data rate, low power, sub-1GHZ transceiver | 1 | U15
2 | 102-00019 | Balun Transformer | A | 50 Ohm Balun to Spirit1 With Integrated Harmonic Filter | 1 | U16
2 | 102-00020 | Crystal 32.768kHz 3.2 x 1.5 x 0.9 mm | A | Crystal 32.768kHz 12.5pF 3.2mm x 1.5 mm SMD 3.2 x 1.5 x 0.9 mm | 1 | Y6
2 | 102-00024 | Crystal 50MHz | A | Crystal Oscillator 50.000MHz 18pF 3.2mm x 2.5mm x 0.9mm | 2 | Y3, Y5
2 | 102-00033 | Crystal 32.768kHz 1.6 x 1.0 x 0.5mm | A | Crystal Oscillator 32.768kHz 12.5pF SMD 1.6 x 1.0 x 0.5mm | 1 | Y2
2 | 102-00038 | MPU 32BIT 160KB | A | IC MPU 32BIT 160KB FLASH 324-LFBGA | 1 | U1
2 | 102-00039 | LPDDR2 SDRAM 4GBIT | A | IC LPDDR2 SDRAM 4GBIT WFBGA | 1 | U2
2 | 102-00041 | PMU CONV/LDO REG | A | IC PMU CONV/LDO REG 32TQFN | 1 | U4
2 | 102-00043 | USB PWR SW HI-SIDE | A | IC USB PWR SW HI-SIDE DL 8NSOIC | 1 | U8
2 | 102-00044 | TVS ARRAY 4-LINE 3.3V | A | IC TVS ARRAY 4-LINE 3.3V 10-SLP | 2 | U21, 22
2 | 102-00046 | MODULE WIFI WILINK | A | MODULE WIFI WILINK 8 Single-Band Combo Module | 1 | U12
2 | 102-00047 | BUS TRANSCEIVER TRI-ST | A | IC BUS TRANSCEIVER TRI-ST SOT-666 | 1 | U13
2 | 102-00049 | SPI Flash 8Mbit 86MHz 3.3V | A | SPI Flash 8Mbit 86MHz 8SOP 3.3V | 1 | U18
2 | 102-00050 | Zigbee Module | A | RF ZIGBEE SMART ENERGY MOD SMD | 1 | U19
2 | 102-00051 | Crystal 12MHZ 20PF | A | Crystal 12MHZ 20PF SMD | 1 | Y1
2 | 102-00052 | Crystal 16MHz | A | Crystal 16MHz 5.0X3.2mm | 1 | Y7
2 | 102-00055 | Crystal 32.768KHZ CMOS | A | Crystal XO 32.768KHZ CMOS SMD | 1 | Y4
2 | 102-00069 | IC CRYPTO 8UDFN | A | IC CRYPTO 8UDFN ATECC508A-MAHDA | 1 | U7
2 | 102-00070 | FLASH 8GBIT | A | IC FLASH 8GBIT 63VFBGA | 1 | U3
2 | 102-00071 | IC ETHERNET SWITCH 3PORT 64-LQFP | A | IC ETHERNET SWITCH 3PORT 64-LQFP | 1 | U9
2 | 102-00073 | IC WATCHDOG TIMER 6-USP | A | IC WATCHDOG TIMER 6-USP | 1 | U20
2 | 103-00010 | Connector COM TYPE A USB | A | Connector COM TYPE A USB DUAL 2X4POS | 1 | J7
2 | 103-00027 | Switch SPST | A | Push Button 0.05A 32V SPST-NO 4.6X2.8mm | 1 | PB1
2 | 103-00028 | SWITCH TACTILE SPST | A | TE Connectivity. SWITCH TACTILE SPST-NO 0.05A 12V | 4 | S1, S3, S4, S6
2 | 103-00029 | SWITCH TACTILE SPST-NO 0.05A 12V | A | SWITCH TACTILE SPST-NO 0.05A 12V | 2 | S2, S5
2 | 103-00031 | Switch Dip Slide 1-Pos 1mm 6V | A | Switch Dip Slide 1-Pos 1mm 6V | 1 | SW1
2 | 103-00039 | TVS DIODE 5VWM 14VC | A | TVS DIODE 5VWM 14VC SC-76/SOD323 | 1 | D3
2 | 103-00040 | TVS DIODE 100VWM 162VC | A | TVS DIODE 100VWM 162VC SMA | 2 | D12, D15
2 | 103-00046 | CONN MAGJACK 1PORT 100 BASE-T | A | CONN MAGJACK 1PORT 100 BASE-T | 2 | P4, P6
2 | 103-00048 | CONN RCPT USB 3.0 MICRO B SMD | A | CONN RCPT USB 3.0 MICRO B SMD | 1 | P1
2 | 103-00049 | FUSE BRD MNT 32VAC/63VDC 1A | A | FUSE BRD MNT 1A 32VAC/63VDC 0603 | 1 | F1
2 | 301-00009 | Control Module PCB | E | Control Module PCB | 1 | PCB1
2 | 510-00001v0.7.1 | Hub Operating Environment | A |  | 1 |  | Hub operating environment (OE) to be programmed to hub flash
2 | 520-00001v1.0.0 | Hub MCU Firmware | A |  | 1 |  | Firmware to be programmed on hub MCU
2 | 530-00003v1.1.9 | Hub Ecovent Application | A |  | 1 |  | Hub Ecovent application to be programmed in operating environment on flash
1 | 800-00004 | Control Hub Ordering Code NSM | E | Control Hub Ordering Code NSM | 1 | A
2 | 103-00001 | Control Hub Foil | B | Copper foil to ground board components on the control module PCB | 1 | B
2 | 201-00044 | Control Hub NSM | B | Control Hub NSM ordering code drawing | 1
2 | 401-00075 | Control Hub Pulp Pack | A | Packaging Assembly - pulp packaging clamshell with rubber bands - holds 1 control hub | 1 |  | Packaging for control hub
3 | 401-00027 | Control Hub Bottom Pulp Molded | A | Packaging - holds 1 control hub - bottom of pulp molded assembly | 1
3 | 401-00028 | Control Hub Top Pulp Molded | A | Packaging - holds 1 control hub - top half of pulp molded assembly | 1
3 | 401-00072 | Rubber Band 8 Inch | A | Packaging - Rubber Band 8" length, .05" thick, .38" wide - used to hold pulp packaging together | 2
2 | 601-00015 | Reset Button Push Tool | A | Reset Button Push Tool | 1 | E
2 | 602-00031 | Control Hub Bottom Plate | C | Control Hub Bottom Plate | 1 | C
2 | 602-00032 | Control Hub Main Housing | H | Control Hub Main Housing | 1 | A
2 | 602-00033 | Control Hub Top Plate | D | Control Hub Top Plate | 1 | D
2 | 602-00131 | Control Hub Light Pipe | B | Control Hub Light Pipe | 1 | F
2 | 603-00007 | Rubber Foot, Clear | A | Rubber Foot, Clear | 4 | G
2 | 603-00020 | Screw M2.5x5 Button Head Plastite | A | Screw M2.5x5 Button Head Plastite | 4 |  | These screws are to be bulk packaged separately with all other screws of this type in the order.
1 | 802-00002 | Cat 5 Ethernet Cable | A | Length: 3' to 5' ft Type: Flat Color: White or Gray | 1 |  | Shipped With Unit
1 | 802-00004 | USB Power Supply and Cable Assembly | A | FCC, IC and ETL controlled part | 1 |  | Shipped With Unit
2 | 802-00001 | USB Power Supply | A | Color: white Input: AC Output: USB 5V | 1 |  | USB Power Supply
2 | 802-00005 | USB 3.0 Cable, A-Male to Micro-B | A | Color: white Type: USB 3.0A, A-Male to Micro-B Length: 5ft | 1 |  | USB Cable

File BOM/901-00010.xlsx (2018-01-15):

level | item_number | item_name | revision | description | quantity | reference_designator | bom_notes
0 | 901-00010 | Wall Sensor, Improved | D | Wall Sensor, Improved RF Performance, Improved Safety
1 | 000-00012 | Label Contents, Wall Sensor Pulp | A | Label Contents, Wall Sensor Pulp packaging | 1 |  | Pulp Packaging Label Contents
1 | 000-00025 | Label Contents, FCC, IC, and ETL Wall Sensor | A | Label Contents with FCC and IC info on the wall sensor | 1 |  | Device Label Contents
1 | 201-00010 | Wall Sensor, Improved | B | Wall Sensor, Improved | 1
1 | 403-00006 | Physical Label, 1x2 | A | Physical Label Material: The polyester label and acrylic permanent adhesive Size: 1x2 Color: White Thermal transfer printable glossy white polyester label stock; pressure-sensitive permanent "Type P", secured by adhesive and approved UL 969 for indoor use, suitable for use on FRPA100X ABS/PC plastic. -40 C to +100 C ETL controlled part | 2 | C | Physical Labels
1 | 801-00001 | Powercore | D | Powercore Added powercore test instructions under the files section | 1 | A
2 | 201-00031 | Powercore | B | Powercore assembly drawing | 1
2 | 701-00012 | Power Core PCA | C | Ecovent power core PCA consists of power core primary and secondary The boards are connected by capacitor C3 and transformer T2 leads Power Core Assembly Instructions attached under the files section | 1 | B
3 | 101-00028 | 2200pF 250VAC RADIAL | B | Capacitor Ceramic 2200pF 250VAC 20% RADIAL | 1 | C3
3 | 103-00003 | Polyester Film Tape - yellow | A | 3M Polyester Film Electrical Tape 56, yellow General purpose polyester tape with thermosetting rubber adgesive Width: 1" Roll size: 216' ETL controlled component | 1 |  | Add tape in two locations (see assembly instructions)
3 | 701-00008 | Power Core Primary PCA | D | Ecovent power core primary PCA Dimensions: 1 in x 1 in Thickness: 68.713 mil | 1
4 | 000-00002 | DNP | A | R1 Do Not Populate | 1 | R1
4 | 101-00027 | 0.33uF 50V 0603 | A | Capacitor Ceramic 0.33uF 50V 10% X7R 0603 | 1 | C4 | PRI
4 | 101-00029 | 6.8uF 400V RADIAL | A | Capacitor Aluminum 6.8uF 400V 20% RADIAL ETL controlled component | 2 | C1,C2 | PRI
4 | 101-00077 | 100 uH 0.32 A | A | Inductor 100 uH 10 % 0.32 A | 1 | L1 | PRI
4 | 101-00101 | 49.9 Ohm 1/16W | A | Resistor 49.9 Ohm 1/16W 1% 0402 SMD | 1 | R2 | PRI
4 | 101-00102 | 49.9 Ohm 1/4W | A | Resistor 49.9 Ohm 1/4W 1% 1206 SMD | 1 | R3 | PRI
4 | 101-00103 | 0.91 Ohm 1/8W | A | Resistor 0.91 Ohm 1/8W 1% 0805 SMD | 1 | R4 | PRI
4 | 101-00104 | 162 kOhm 1/16W | A | Resistor 162 kOhm 1/16W 1% 0402 SMD | 1 | R5 | PRI
4 | 101-00105 | 1.78 kOhm 1/16W | A | Resistor 1.78 kOhm 1/16W 1% 0402 SMD | 1 | R6 | PRI
4 | 101-00106 | 38.3 kOhm 1/16W | A | Resistor 38.3 kOhm 1/16W 1% 0402 SMD | 1 | R8 | PRI
4 | 101-00131 | Flyback Transformer | A | Transformer, Discontinuous Mode Flyback, Â±7% ETL controlled component | 1 | T2 | PRI
4 | 102-00002 | DIODE 1000V 1A | A | DIODE GEN PURPOSE 1000V 1A SMA | 1 | D3 | PRI
4 | 102-00003 | DIODE SWITCHING 200V 0.2A | A | DIODE SWITCHING 200V 0.2A SOD323 | 1 | D5 | PRI
4 | 102-00012 | MOSFET N-channel | A | MOSFET N-CH 600V 2.5A TO252 | 1 | Q1 | PRI
4 | 102-00036 | Rectifier Bridge 600V 0.5A | A | Rectifier Bridge GP 600V 0.5A MINIDIP | 1 | D2 | PRI
4 | 102-00037 | Flyback power supply controllers | A | IC REG CTRLR FLYBK ISO 7SOIC | 1 | U1 | PRI
4 | 103-00037 | FUSE SLOW 250VAC 500mA | A | FUSE SLOW 250VAC 500mA RADIAL | 1 | F2 | PRI
4 | 103-00044 | TVS DIODE 146VC | A | TVS DIODE 90VWM 146VC SMA | 1 | D1 | PRI
4 | 301-00005 | Power Core Primary PCB | C | Power Core Primary PCB Dimensions: 1 in x 1 in Thickness: 1.745 mm Temperature: 130 C min Flammability: V-0 ETL controlled component | 1 | PCB2 | PRI
4 | 801-00049 | Cable, Power Core AC, 1.5 in Wire, Circular Crimp on 1 side | G | Wiring from high voltage rail to power core primary Circular crimp on one side of the wire Wire length is 1.5" +/- 0.15" | 2
5 | 101-00146 | Wire 24 Awg, Solid Core, 1.5in, UL rated | D | Wire Gauge: 24 awg Voltage: 300 V min. Color: black Temperature: 80 C min Flammability: VW-1 Insulation: PVC Nominal overall diameter 0.052 in Length 1.5" +/- 0.15" UL 1007/1569 rated RoHS compliant ETL controlled component | 1 | B
5 | 101-00147 | Circular Terminal, 22-26 AWG, M2.5 screw | B | Circular Terminal, 22-26 AWG, M2.5 screw | 1 | A
5 | 201-00079 | Cable, Power Core AC, 1.5 in Wire, Circular Crimp on 1 side | B | Cable, Power Core AC, 1.5 in Wire, Circular Crimp on 1 side | 1
3 | 701-00013 | Power Core Secondary PCA | C | Ecovent power core secondary PCA. Dimensions: 1.478 in x 1 in Thickness: 68.713 mil | 1
4 | 000-00004 | DNP - C, L, R | A | Do Not Populate - C203, C201, L31, R15, R82, R105, R203, R204, R205, R206, R207, R208, R19, R20, R100, R104, R202, R25, R92, R97, R163, R165, R166, R167, R168, R169, R170, R171, R84 | 0 | R4,R5,R6,R2,R3,P3,J1 | SEC
4 | 101-00025 | 820uF 6.3V Radial | A | Capacitor Aluminum 820uF 6.3V 20% Radial ETL controlled component | 2 | C1,C2 | SEC
4 | 101-00026 | 1uF 16V 0402 | A | Capacitor Ceramic 1uF 16V 10% X5R 0402 | 2 | C3,C4 | SEC
4 | 101-00076 | 1.5 uH, 2.5 A, Â±20% | A | Power Inductor, 1.5 uH, 2.2 A, Â±20% | 1 | L1 | SEC
4 | 101-00099 | 2.61 kOhm 1/16W | A | Resistor 2.61 kOhm 1/16W 1% 0402 SMD | 1 | R1 | SEC
4 | 101-00156 | 1000pf 50V 10% X7R 0402 | A | CAP CER 1000PF 50V 10% X7R 0402 | 1 | C5 | SEC
4 | 101-00157 | 1 Ohm 5% 1/8W 0805 | A | RES SMD 1 OHM 5% 1/8W 0805 | 1 | R2 | SEC
4 | 102-00001 | DIODE SBR 45V 10A | A | DIODE SBR 45V 10A POWERDI5 | 1 | D1 | SEC
4 | 103-00050 | Female 4 pin connector 28 awg | A | Female 4 pin connector 28 awg | 2 | P1, P2 | SEC
4 | 301-00011 | Power Core Secondary PCB | C | Power Core Secondary PCB Dimensions: 1.478 in x 1 in Thickness: 1.745 mm Temperature: 130 C min Flammability: V-0 ETL controlled component | 1 | PCB1 | SEC
2 | 800-00001 | Powercore Ordering Code NSM | E | Powercore Ordering Code NSM | 1 | A
3 | 201-00034 | Powercore NSM | B | Powercore NSM ordering code drawing | 1
3 | 602-00001 | Powercore Front Plate | D | Powercore Front Plate | 1 | A
3 | 602-00002 | Powercore Housing | J | Powercore Housing | 1 | B
3 | 602-00003 | Powercore Assembly Tab | B | Powercore Assembly Tab | 3 | D
3 | 603-00001 | Screw M2.5x6 Plastite 45 | A | Screw M2.5x6 Plastite 45 | 3 |  | These screws are to be bulk packaged separately with all other screws of this type in the order.
3 | 603-00001 | Screw M2.5x6 Plastite 45 | A | Screw M2.5x6 Plastite 45 | 3 | E
3 | 801-00003 | Powercore Hot Side | C | Powercore Hot Side Assembled | 1 | C
4 | 201-00033 | Powercore Hot Side | B | Powercore Hot Side | 1
4 | 601-00001 | Bent Prong Hot Side | A | NEMA style prong for hot side | 1 | B
4 | 601-00003 | Receptical Bronze Hot Side | B | Female receptical bronze hot side | 1 | A
3 | 801-00004 | Powercore Neutral Side | D | Powercore Neutral Side Assembled | 1 | G
4 | 201-00030 | Powercore Neutral Side | B | Powercore Neutral Side | 1
4 | 601-00002 | Bent Prong Neutral Side | A | NEMA style prong for neutral side | 1 | B
4 | 601-00004 | Receptical Bronze Neutral Side | B | Female receptical bronze neutral side | 1 | A
3 | 801-00005 | Powercore Ground | E | Powercore Ground Assembled | 1 | F
4 | 101-00039 | Wire 14 awg, UL Rated | A | Wire Gauge: 14 awg Voltage: 300V min. Color: Green Temperature: 90 C min Flammability: VW-1 Safety: UL11028 ETL controlled component | 2.5 | C | connecting wire between ground receptacles
4 | 201-00035 | Powercore Ground | B | Powercore Ground Assembly Drawing | 1
4 | 601-00005 | Receptical Bronze Upper Ground | E | Female receptical bronze upper ground | 1 | A
4 | 601-00006 | Receptical Bronze Lower Ground | D | Female receptical bronze lower ground | 1 | D
4 | 601-00013 | Ground Prong | A | NEMA style prong for ground | 1 | B
1 | 801-00039 | Wall Sensor Ring, Improved RF Performance | B | Sensor Ring Assembly with Improved RF Performance PCA | 1 | B
2 | 201-00069 | Wall Sensor Ring, Improved RF Performance | B | Wall Sensor Ring, Improved RF Performance Assembly Drawing | 1
2 | 701-00003 | Wall Sensor Ring PCA, Improved RF Performance | B | Wall Sensor Ring PCA Improved RF Performance | 1 | B
3 | 101-00001 | Antenna Mitsubishi | A | Mitsubishi SMD Chip Antenna 3.0X10.5mm | 1 | A2
3 | 101-00002 | Chip Antenna | A | Bluetooth / WLAN / WiFi Ceramic Chip Antenna | 1 | A1
3 | 101-00005 | 0.1uF 16V 1005 (0402) | A | Capacitor Ceramic 0.1uF 16V X7R 10% 1005 (0402) | 20 | C1, C2, C5, C11, C13, C14, C15, C16, C20, C28, C33, C36, C38, C40, C49, C52, C53, C54, C59, C60
3 | 101-00006 | 1uF 10V 1005 (0402) | A | Capacitor Ceramic 1uF 10V X5R 10% 1005 (0402) | 2 | C19, C39
3 | 101-00007 | 10uF 10V 1608 (0603) | A | Capacitor Ceramic 10uF 10V X5R 20% 1608 (0603) | 4 | C17, C18, C21, C34
3 | 101-00008 | 10nF 10V 1005 (0402) | A | Capacitor Ceramic 10nF 10V X7R 10% 0402 (1005) | 1 | C22
3 | 101-00009 | 12pF 50V 1005 (0402) | A | Capacitor Ceramic 12pF 50V C0G 5% 1005 (0402) | 2 | C8, C9
3 | 101-00010 | 27pF 50V 1005 (0402) | A | Capacitor Ceramic 27pF 50V NP0 5% 1005 (0402) | 2 | C25, C26
3 | 101-00013 | 100pF 16V 0402 (1005) | A | Capacitor Ceramic 100pF 16V C0G 10% 0402 (1005) | 3 | C32, C35, C37
3 | 101-00014 | 330pF 50V 1005 (0402) | A | Capacitor Ceramic 330pF 50V C0G 5% 1005 (0402) | 1 | C41
3 | 101-00016 | 220pF 50V 1005 (0402) | A | Capacitor Ceramic 220pF 50V C0G 5%1005 (0402) | 2 | C43, C46
3 | 101-00017 | 0.47uF 200V 1812 | A | Capacitor Ceramic 0.47uF 200V X7R 10% 1812 | 2 | C55, C57
3 | 101-00018 | 10uF 16V 2012 (0805) | A | Capacitor Ceramic 10uF 16V X5R 10% 2012 (0805) | 6 | C27, C29, C30, C31, C47, C50
3 | 101-00019 | 47uF 10V 3216 (1206) | A | Capacitor Ceramic 47uF 10V X5R 20% 3216 (1206) | 2 | C51, C61
3 | 101-00020 | 1nF 50V 1005 (0402) | B | Capacitor Ceramic 1nF 50V X7R 10% 1005 (0402) | 9 | C3, C62, C63, C65, C66, C67, C68, C69, C70
3 | 101-00021 | 2.2nF 50V 1005 (0402) | A | Capacitor Ceramic 2.2nF 50V X7R 5% 1005 (0402) | 1 | C12
3 | 101-00022 | 47nF 10V 1005 (0402) | A | Capacitor Ceramic 47nF 10V X7R 10% 1005 (0402) | 1 | C4
3 | 101-00044 | 9.5nH Wirewound 0603 | A | Inductor 9.5nH 650mA 0.5nH 0603 SMD Wirewound | 1 | L8
3 | 101-00048 | 30pF 50V 0402 | A | Capacitor Ceramic 30pF 50V 5% NP0 0402 | 2 | C42, C44
3 | 101-00050 | 7pF 50V 1005 (0402) | A | Capacitor Ceramic 7pF 50V COG 0.5pF 1005 (0402)` | 4 | C6, C7, C23, C24
3 | 101-00051 | 0.8pF 50V 1005 (0402) | A | Capacitor Ceramic 0.8pF 50V NPO 1005 (0402) | 1 | C10
3 | 101-00058 | Choke CM 1400 Ohm | A | CHOKE COMMON MODE 1400 OHM SMD | 3 | CM1, CM2, CM3
3 | 101-00059 | Ferrite Bead 220 Ohm | A | FERRITE BEAD 220 Ohm 800mA 0402 | 2 | L1, L10
3 | 101-00061 | 18nH Wirewound 0603 | A | Inductor 18nH 550mA 0603 SMD Wirewound | 1 | L7
3 | 101-00063 | 2.2uH 510mA 1007 | A | Inductor 2.2uH 510mA 20% 1007 | 1 | L2
3 | 101-00064 | 68nH Wirewound 0603 | A | Inductor 68nH 340mA 0603 SMD Wirewound | 1 | L9
3 | 101-00066 | 10uH 100mA 0805 | A | Inductor 10uH 100mA 20% 0805 SMD | 1 | L3
3 | 101-00067 | 27nH 300mA 0402 | A | Inductor 27nH 300mA 5% 0402 SMD | 1 | L4
3 | 101-00068 | 100nH 150mA 0402 | A | Inductor 100nH 150mA 5% 0402 SMD | 1 | L5
3 | 101-00082 | 100 kOhm 1/16W | A | Resistor 100 kOhm 1/16W 1% 1005 (0402) | 3 | R16, R18, R45
3 | 101-00092 | 0 Ohm 1/10W | A | Resistor 0 Ohm 1/10W 1608 (0603) | 4 | R41, R56, R57, R60
3 | 101-00097 | 10 kOhm 1/16W | A | Resistor 10 kOhm 1/16W 1% 1005 (0402) | 11 | R6, R7, R8, R13, R21, R23, R24, R25, R26, R27, R63
3 | 101-00126 | 75 kOhm 1/16W | A | Resistor 75 kOhm 1/16W 1% 1005 (0402) | 1 | R50
3 | 101-00127 | 47.5 kOhm 1/16W | A | Resistor 47.5 kOhm 1/16W 1% 1005 (0402) | 1 | R64
3 | 101-00128 | 22 Ohm 1/10W | A | Resistor 22 Ohm 1/10W 1% 0402 SMD | 21 | R1, R2, R4, R5, R9, R10, R11, R19, R22, R31, R32, R34, R42, R43, R46, R53, R54, R58, R59, R61, R62
3 | 101-00158 | 100uF 10V X5R 20% (1206) | A | Capacitor CER 100uF 10V X5R 20% (1206) | 2 | C45, C64
3 | 101-00165 | 1 Ohm 5% 1/10W 0402 | A | RES SMD 1 OHM 5% 1/10W 0402 | 1 | R29
3 | 101-00167 | 33 Ohm 5% 1/10W 0402 | A | RES SMD 33 OHM 5% 1/10W 0402 | 1 | R30
3 | 101-00171 | 24 Ohm 5% 1/10W 0402 | A | RES SMD 24 OHM 5% 1/10W 0402 | 1 | R44
3 | 102-00008 | LED RGB Square SMD | A | Led RGB Square Clear 1.0X1.0mm | 1 | D2
3 | 102-00015 | SPIRIT1 RF Transceiver | A | QFN20, Low data rate, low power, sub-1GHZ transceiver | 1 | U5
3 | 102-00017 | Regulator Buck Adj 300mA | A | 360nA Iq Step Down Converter for Low Power Applications, 12WSON | 1 | U4
3 | 102-00019 | Balun Transformer | A | 50 Ohm Balun to Spirit1 With Integrated Harmonic Filter | 1 | U6
3 | 102-00022 | Crystal 32.768kHz 7pF 3.2 x 1.5 x 0.9 mm | A | Crystal Oscillator 32.768kHz 7pF 3.2 x 1.5 x 0.9 mm SMD | 2 | Y1, Y3
3 | 102-00024 | Crystal 50MHz | A | Crystal Oscillator 50.000MHz 18pF 3.2mm x 2.5mm x 0.9mm | 1 | Y5
3 | 102-00026 | Balun to nRF51822-QFAA | A | 50 ohm balun transformer for 2.45GHz ISM QFN Package | 1 | B1
3 | 102-00027 | SoC 2.4GHz QFAA | A | 2.4GHz proprietary system-on-chip 256K FLASH 48VFQFN | 1 | U1
3 | 102-00028 | MCU | A | 32-bit MCU ARM, 64-Pin, 256kB flash, Connectivity line | 1 | U2
3 | 102-00029 | SPI Flash 3.3V | A | SPI Flash 8Mbit 75 MHz 3.3V | 1 | U3
3 | 102-00034 | Crystal 16MHz | A | Crystal Oscillator 16MHz 8pF SMD 2.0 x 1.6 x 0.5 mm | 1 | Y2
3 | 102-00035 | Crystal 25MHz | A | Crystal Oscillator 25MHz 18pF SMD 5.0 x 3.2 x 1.3 mm | 1 | Y4
3 | 102-00058 | USB Desicated Charging Port Controller | A | IC USB PWR SW/CTRLR CHRG 8MSOP | 1 | U7
3 | 102-00060 | USB Charging Port Power Switch and Controller | A | IC USB CHARGING CTLR SW 16VFQFPN | 1 | U9
3 | 103-00006 | USB | A | Conn RCPT USB-A 4POS SMD RA HOR | 2 | P4, P5
3 | 103-00015 | Header, 4-Pin | A | 100mil, 8.08mm Head Length | 2 | P1, P2
3 | 103-00016 | Molex Connector Male socket 4 position | A | Molex Connector Male socket 4 position Pico-EZMate series Mating view: Height: 1.55 mm Width: 4.5 mm Length: 6.6 mm | 2 | P3, P8
3 | 103-00029 | SWITCH TACTILE SPST-NO 0.05A 12V | A | SWITCH TACTILE SPST-NO 0.05A 12V | 1 | S1
3 | 103-00032 | Varistor 5.5V | A | VARISTOR TVS MULTI 5.5V 20A 0402 (1005) | 1 | R14
3 | 103-00033 | TVS Diode 5.3V | A | TVS DIODE 5.3V UNIDIR TSLP-2-17 | 1 | D1
3 | 103-00034 | TVS Diode 6V | A | TVS DIODE 200W SOD-123F 6.0V | 1 | TVS1
3 | 103-00035 | ESD-protection diode | A | Low Capacitance Double Rail to Rail 15kV ESD Protection Diode | 1 | U10
3 | 201-00029 | Wall Sensor PCB Assembly Drawing | A |  | 1
3 | 301-00010 | Wall Sensor Ring PCB | E | Wall Sensor Ring PCB | 1 | PCB1
3 | 520-00007v1.0.8 | Wall Sensor Firmware | A |  | 1 |  | Firmware to be programmed on wall sensor
2 | 701-00009 | Pressure Sensor PCA | D | Pressure Sensor PCA (pressure and temperature) NO CLEAN | 1 | C
3 | 101-00005 | 0.1uF 16V 1005 (0402) | A | Capacitor Ceramic 0.1uF 16V X7R 10% 1005 (0402) | 1 | C1
3 | 101-00007 | 10uF 10V 1608 (0603) | A | Capacitor Ceramic 10uF 10V X5R 20% 1608 (0603) | 2 | C2, C3
3 | 101-00097 | 10 kOhm 1/16W | A | Resistor 10 kOhm 1/16W 1% 1005 (0402) | 2 | R1, R3
3 | 101-00128 | 22 Ohm 1/10W | A | Resistor 22 Ohm 1/10W 1% 0402 SMD | 1 | R6
3 | 102-00056 | MEMS Pressure Sensor | A | IC MEMS Pressure Sensor 10HCLGA | 1 | U1
3 | 103-00016 | Molex Connector Male socket 4 position | A | Molex Connector Male socket 4 position Pico-EZMate series Mating view: Height: 1.55 mm Width: 4.5 mm Length: 6.6 mm | 1 | P1
3 | 301-00004 | Pressure Sensor PCB | D | Pressure Sensor PCB | 1 | PCB1
2 | 701-00010 | Temperature Sensor PCA | C | Temperature Sensor PCA (temperature and humidity) NO CLEAN | 1 | D
3 | 101-00005 | 0.1uF 16V 1005 (0402) | A | Capacitor Ceramic 0.1uF 16V X7R 10% 1005 (0402) | 1 | C2
3 | 101-00007 | 10uF 10V 1608 (0603) | A | Capacitor Ceramic 10uF 10V X5R 20% 1608 (0603) | 2 | C1, C3
3 | 101-00084 | 0 Ohm 1/16W | A | Resistor 0 Ohm 1/16W 0402 (1005) | 2 | R3, R5
3 | 101-00128 | 22 Ohm 1/10W | A | Resistor 22 Ohm 1/10W 1% 0402 SMD | 1 | R4
3 | 102-00066 | Temperature sensor RH 3% DFN | A | I2C Humidity and Temperature Sensor | 1 | U1
3 | 103-00016 | Molex Connector Male socket 4 position | A | Molex Connector Male socket 4 position Pico-EZMate series Mating view: Height: 1.55 mm Width: 4.5 mm Length: 6.6 mm | 1 | P1
3 | 301-00008 | Temperature Sensor PCB | C | Temperature Sensor PCB | 1 | PCB1
2 | 800-00002 | Wall Sensor Ring Ordering Code NSM | E | Wall Sensor Ring Ordering Code NSM | 1 | A
3 | 201-00043 | Wall Sensor Ring NSM | B | Wall Sensor Ring NSM | 1
3 | 401-00074 | Wall Sensor Pulp Pack | A | Packaging Assembly - pulp packaging clamshell with rubber bands - holds 1 wall sensor | 1 |  | Packaging for wall sensor. Both sensor ring and powercore go inside packaging.
4 | 401-00025 | Wall Sensor Bottom Pulp Molded | A | Pulp molded packaging - holds 1 wall sensor - bottom half of pulp molded assembly | 1
4 | 401-00026 | Wall Sensor Top Pulp Molded | A | Packaging - holds 1 wall sensor - top half of pulp molded assembly | 1
4 | 401-00072 | Rubber Band 8 Inch | A | Packaging - Rubber Band 8" length, .05" thick, .38" wide - used to hold pulp packaging together | 2
3 | 602-00004 | Wall Sensor Ring Back | F | Sensor Ring Back | 1 | C
3 | 602-00005 | Wall Sensor Ring Front | C | Sensor Ring Front | 1 | A
3 | 602-00129 | Wall Sensor Light Pipe | B | Wall Sensor Light Pipe | 1 | B
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

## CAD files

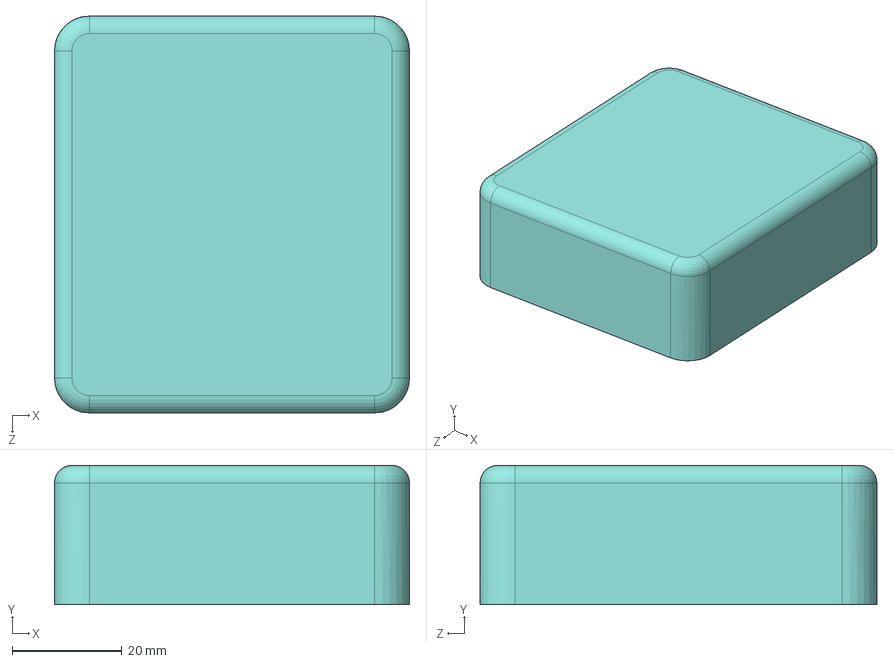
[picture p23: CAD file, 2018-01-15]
New Damper Concept_CAD/SolidWorks 17 CAD Database/Power Module.SLDASM
64.8 x 25.4 x 72.4 mm
Power Module Case
AA Batt x 4
K&J DH21 Magnet x 2

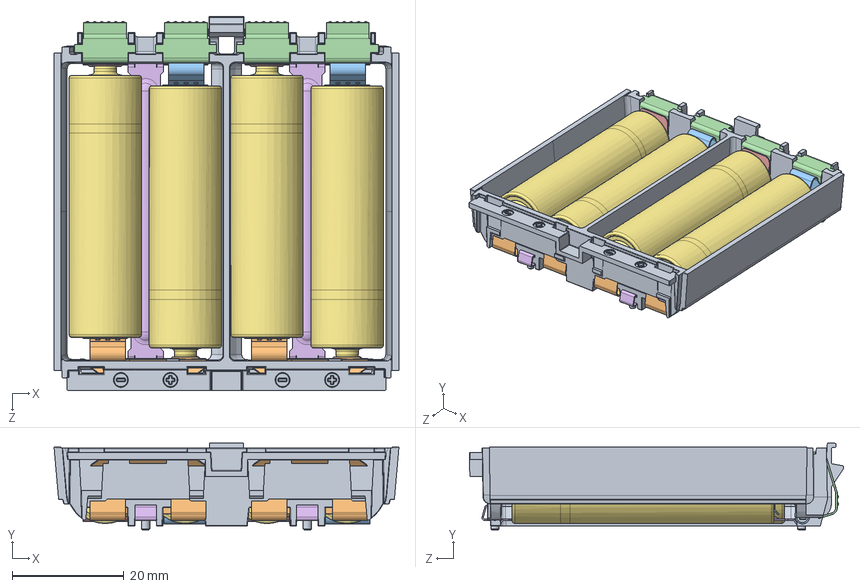
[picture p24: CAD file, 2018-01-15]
New Damper Concept_CAD/SolidWorks 17 CAD Database/801-00020.SLDASM
61.9 x 15.5 x 67.1 mm
AA Batt x 4

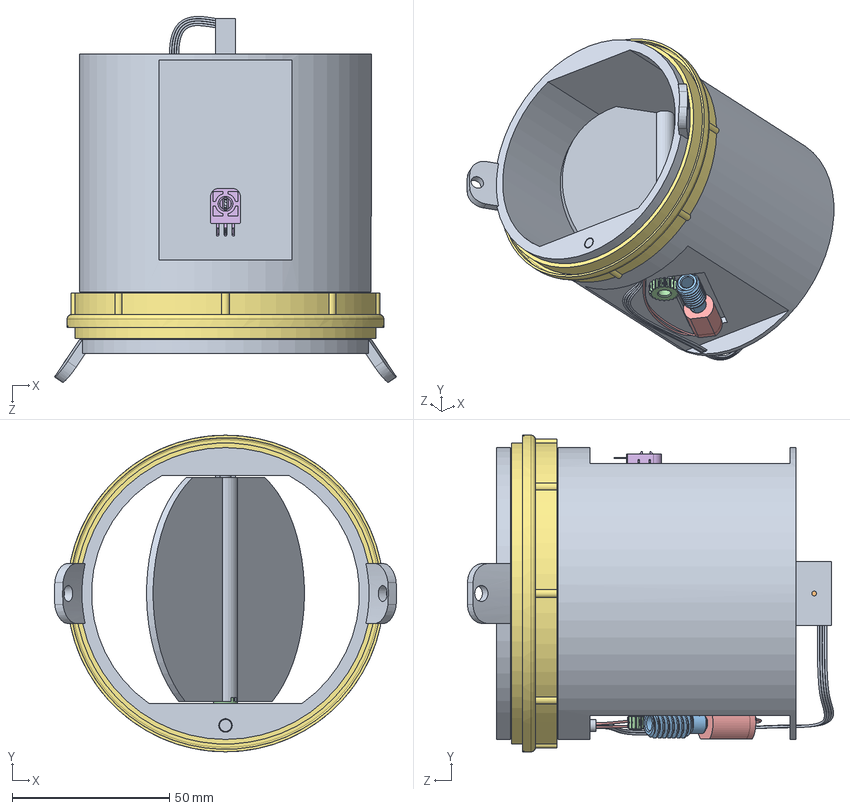
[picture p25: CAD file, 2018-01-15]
New Damper Concept_CAD/SolidWorks 17 CAD Database/Damper Assy.SLDASM
108.7 x 100.6 x 116.3 mm
Butterfly Damper, Master
Pressure Sensor PCBA
B004N6356S worm
B004N84ZKQ worm gear
Mabuchi FF-N20WA-9Z190
Polyshine F10k-b10kh0
Custom Gasket

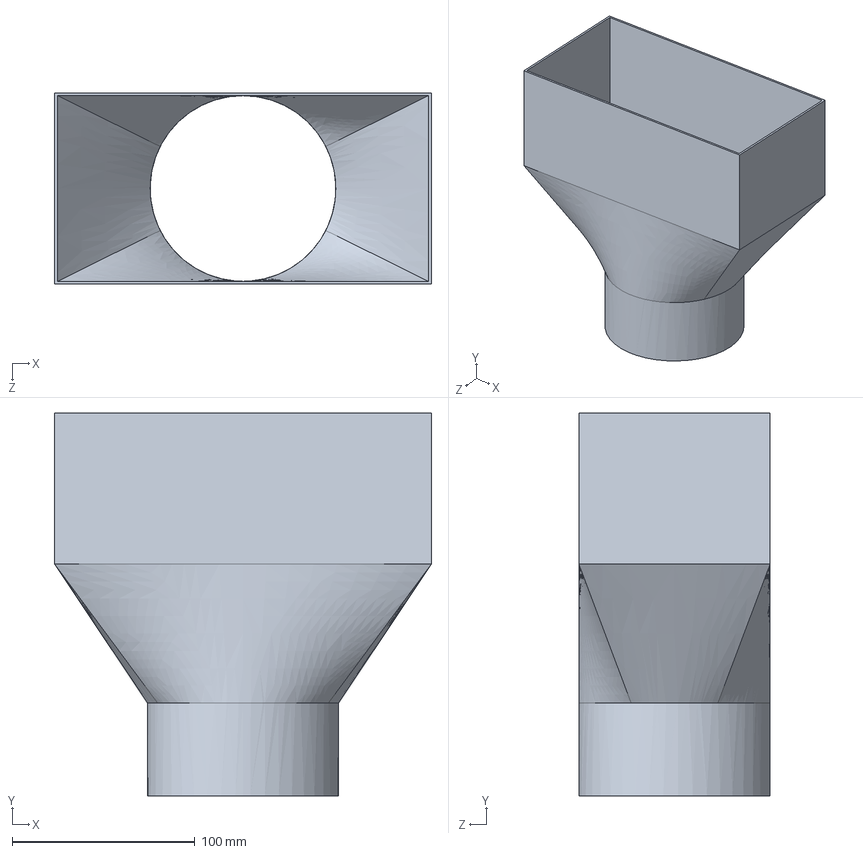
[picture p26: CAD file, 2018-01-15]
New Damper Concept_CAD/SolidWorks 17 CAD Database/Boot 8x4x4.SLDPRT
206.4 x 209.5 x 104.8 mm

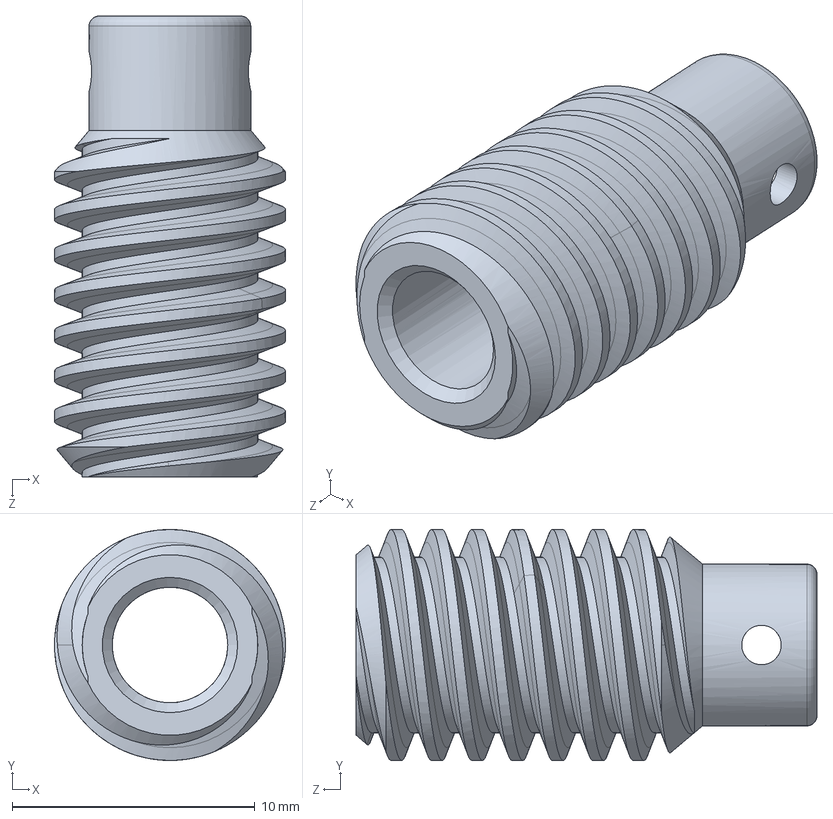
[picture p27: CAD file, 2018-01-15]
New Damper Concept_CAD/SolidWorks 17 CAD Database/B004N6356S worm.sldprt
9.52 x 9.52 x 19.0 mm

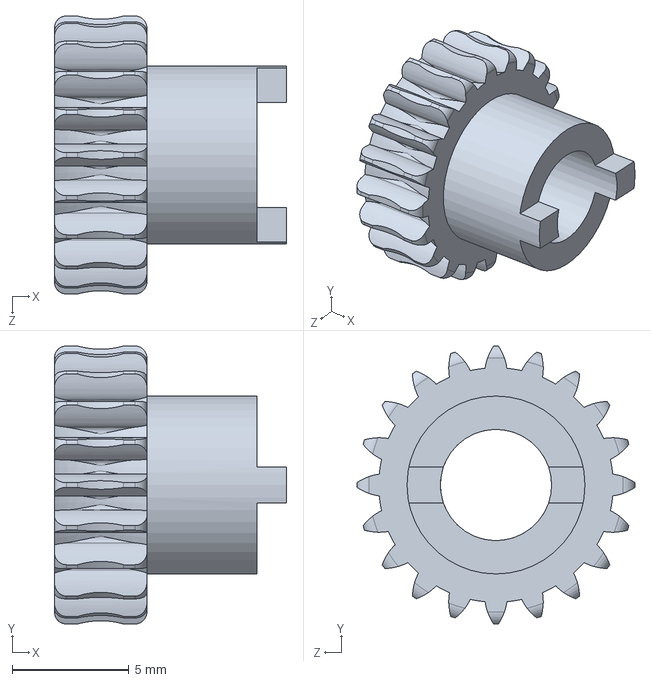
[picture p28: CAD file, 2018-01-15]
New Damper Concept_CAD/SolidWorks 17 CAD Database/B004N84ZKQ worm gear.sldprt
9.94 x 11.9 x 11.9 mm

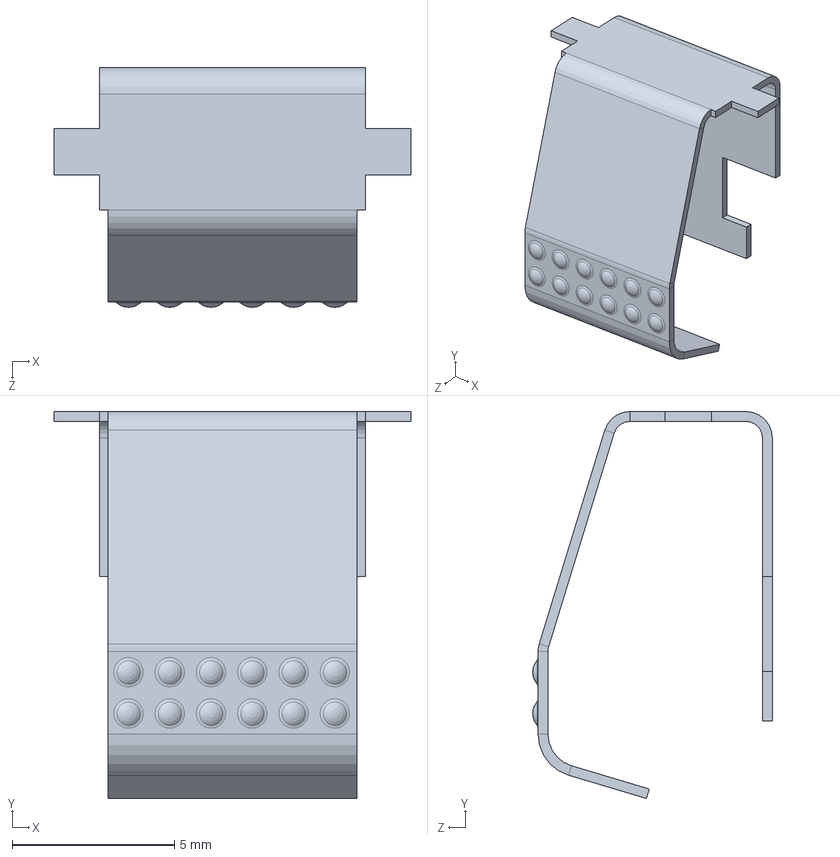
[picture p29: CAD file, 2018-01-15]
New Damper Concept_CAD/SolidWorks 17 CAD Database/601-00014.SLDPRT
11.0 x 11.9 x 7.38 mm

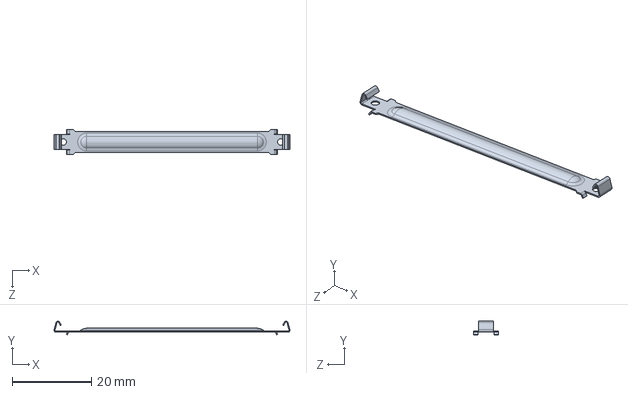
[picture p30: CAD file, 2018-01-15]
New Damper Concept_CAD/SolidWorks 17 CAD Database/601-00018.SLDPRT
59.7 x 3.45 x 6.35 mm

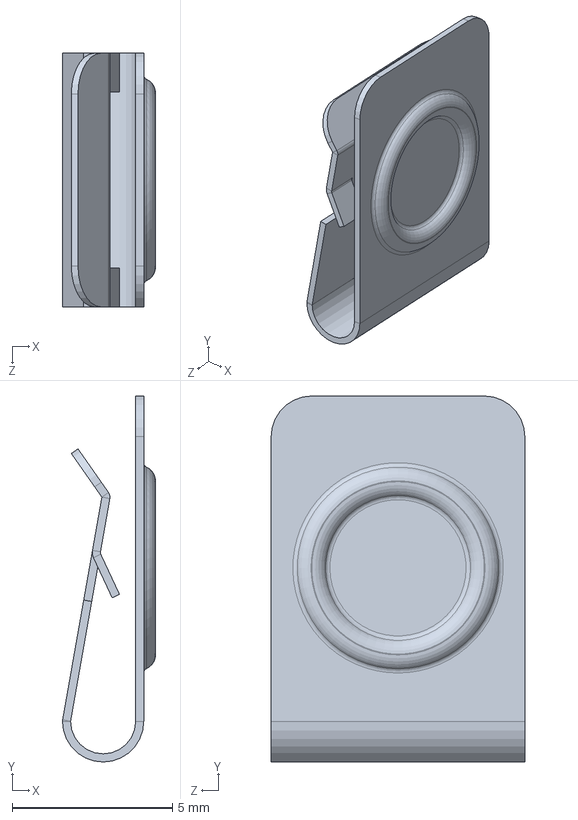
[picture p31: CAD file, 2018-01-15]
New Damper Concept_CAD/SolidWorks 17 CAD Database/601-00016.SLDPRT
2.91 x 11.4 x 7.92 mm

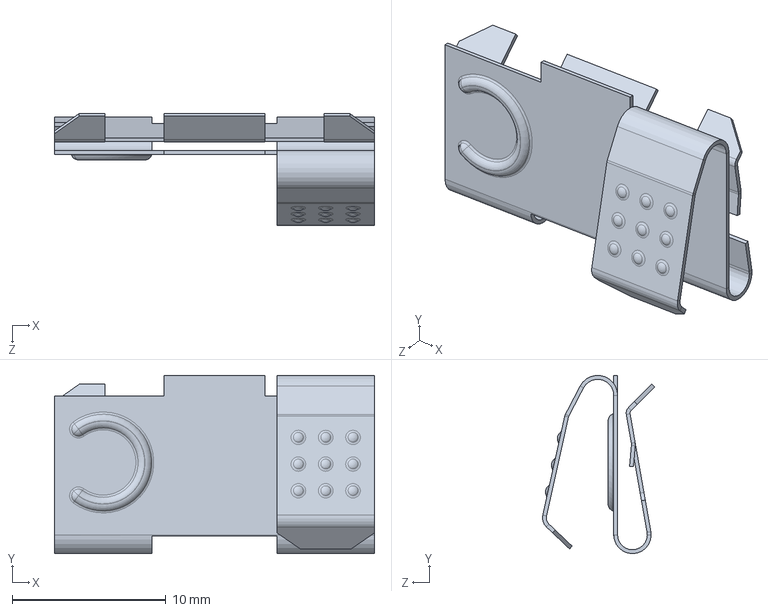
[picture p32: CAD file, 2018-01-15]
New Damper Concept_CAD/SolidWorks 17 CAD Database/601-00007.SLDPRT
20.8 x 11.6 x 7.29 mm

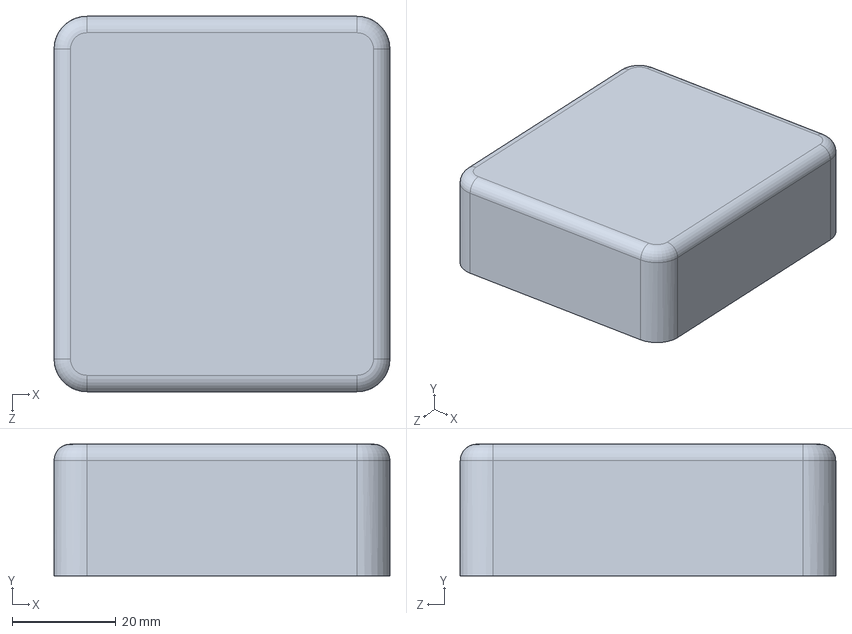
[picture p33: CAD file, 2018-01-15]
New Damper Concept_CAD/SolidWorks 17 CAD Database/Power Module Case.SLDPRT
64.8 x 25.4 x 72.4 mm

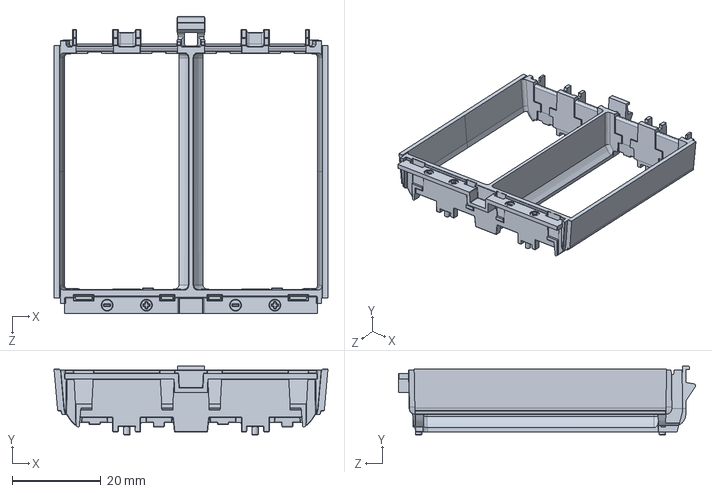
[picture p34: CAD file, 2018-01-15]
New Damper Concept_CAD/SolidWorks 17 CAD Database/602-00060.SLDPRT
61.9 x 15.5 x 67.1 mm

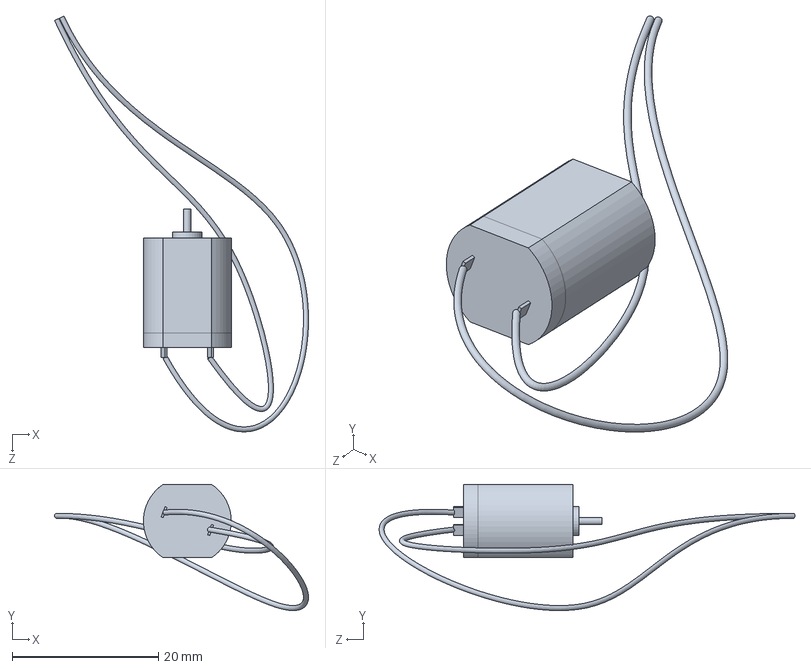
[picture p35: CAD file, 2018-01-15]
New Damper Concept_CAD/SolidWorks 17 CAD Database/Mabuchi FF-N20WA-9Z190.SLDPRT
34.7 x 17.2 x 56.8 mm

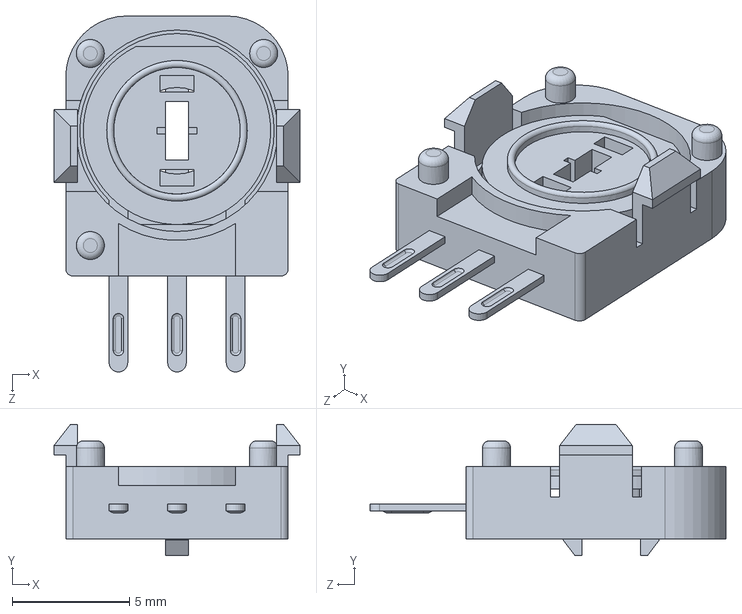
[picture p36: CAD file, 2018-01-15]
New Damper Concept_CAD/SolidWorks 17 CAD Database/Polyshine F10k-b10kh0.SLDPRT
10.5 x 5.60 x 15.2 mm

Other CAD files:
New Damper Concept_CAD/SolidWorks 17 CAD Database/Power Module Wires.SLDPRT
New Damper Concept_CAD/SolidWorks 17 CAD Database/Custom Gasket.SLDPRT
New Damper Concept_CAD/SolidWorks 17 CAD Database/K&J DH21 Magnet.SLDPRT
New Damper Concept_CAD/SolidWorks 17 CAD Database/AA Batt.SLDPRT
New Damper Concept_CAD/SolidWorks 17 CAD Database/601-00010.SLDPRT
New Damper Concept_CAD/SolidWorks 17 CAD Database/90190A170_PAN HEAD PHILLIPS SCREW FOR SHEET METAL.SLDPRT
New Damper Concept_CAD/SolidWorks 17 CAD Database/Butterfly Damper, Master.SLDPRT
New Damper Concept_CAD/SolidWorks 17 CAD Database/Flex Ducting.SLDPRT
New Damper Concept_CAD/SolidWorks 17 CAD Database/Pressure Sensor PCBA.SLDPRT

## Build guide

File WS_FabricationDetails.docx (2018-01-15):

WS:

Number of layers: 4
Dimensions: 77.3x127.47mm
Material type: FR4Tg130
Finish plating: ENIG
Inner copper Wt: 1 oz
Gold finger: no
Thickness: 1.75mm
Array: yes
Array Dim: 235x441mm
No. of boards/array: 12
X-out not allowed:
X-out Qty:
Outer copper Wt. 1.5 oz
Board Spec:
Min. Trace/Space: 0.2/0.1mm

ITAR:
Counterbore:
Countersink:
Soldermask: Top/Bottom green
RoHS: yes
Peelable Mask: No
Plated Slots: No
Controlled dielectric:
Controlled impedance: Yes, 10%

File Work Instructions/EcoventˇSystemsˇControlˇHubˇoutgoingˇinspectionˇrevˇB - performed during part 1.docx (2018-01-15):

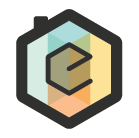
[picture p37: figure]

Ecovent Systems

Control Hub Outgoing Inspection Criteria

800-00004 Control Hub出货前检验标准

Date and Time（日期和时间）: ____________________

Production Lot Number and Quantity（生产批号和数量）: ______________

Part Number（产品编号）: _____________________

Part Description（产品描述）: ________________________

Part Color（产品颜色）: ________________________

Item | Inspection Step 检测步骤 | Inspected By 检测员 | Quantity Passed 合格数量 | Quantity Failed 不合格数量
1 | Inspect Hub housing and covers for dents, scratches, marks, excessive flash, underfill, etc. 检查控制集线器外壳和盖子没有凹痕，划痕，印记，披锋，缺胶等。
2 | Inspect hub cutouts to ensure the foil is well-centered and all cutouts are fully accessible, and foil isn’t visible from directly behind the housing. 检查掏胶口处，要确保金属泊片完全对齐，不能看到金属切泊片。
3 | Inspect heat staked posts to ensure proper deformation, orientation, and seating of cover onto housing. The top plate shall not move with respect to the hub main housing and shall be level with the housing. 检查热融正确，方向正确，盖子要盖好。面板（602-00033）不会与主壳（602-00032）一起动，两个应该齐平的。
4 | Verify Reset tool is installed in assembly. Reset tool is not damaged or bent. 检查Reset tool（601-00015 五金件）已经装好，601-00015 五金件没有损坏或者弯曲。
5 | Inspect control hub bottom plate for rubber feet presence and seating. 检查control hub bottom plate(下盖)装好橡胶脚.
6 | Inspect for presence, orientation, and seating of light pipe. 检查Light Pipe(灯管，602-00131)的装置，及方向。
7 | Make sure the Control Hub is correctly packaged in bubble bag with label that contains the part number and “made in china”
8 | Ensure box part number, quantity, and label matches the contents 确认每个包装的产品编号，数量和标签要与实际物品一致。
9
10
11
12
13

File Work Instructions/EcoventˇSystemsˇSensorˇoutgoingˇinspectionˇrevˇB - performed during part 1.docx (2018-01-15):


Ecovent Systems

Wall Sensor Outgoing Inspection Criteria

800-00001 & 800-00002 Wall Sensor出货前检验标准

Date and Time（日期和时间）: ____________________

Production Lot Number and Quantity（生产批号和数量）: ______________

Part Number（产品编号）: _____________________

Part Description（产品描述）: ________________________

Part Color（产品颜色）: ________________________

Item | Inspection Step检测步骤 | Inspected By 检测员 | Quantity Passed 合格数量 | Quantity Failed 不合格数量
1 | Verify all assembly tabs are inserted and properly seated and oriented, and can be turned by hand. 检查所有安装扣钮（602-00003）正确装好，并能手动转动。
2 | Verify ground assembly is installed and properly seated with one screw installed to a torque of 80 +/- 4 in-oz. Verify no bending of the parts. 检查ground assembly（801-00005）用一颗螺丝将它正确装入好，扭至80 +/- 4 in-oz，检查产品没有弯曲。
3 | Verify hot and neutral side terminals are properly installed, seated, and assembled with the bottom screws only, installed to a torque of 80 +/- 4 in-oz. Verify no bending of the parts. 检查hot and neutral（801-00003,801-00004）的终端口正确安装好，只用下面的螺丝组装，扭至80 +/- 4 in-oz.检查产品没有弯曲。
4 | Inspect wall sensor ring front for cracks, dents, scratches, discoloration, excessive flash, or underfill 检查wall sensor ring front （602-00005）产品的裂缝，凹痕，划伤，污点或者缺胶。
5 | Inspect wall sensor ring back for cracks, dents, scratches, discoloration, excessive flash, or underfill 检查wall sensor ring back （602-00004）产品的裂缝，凹痕，划伤，污点或者缺胶。
6 | Inspect powercore front plate for cracks, dents, scratches, discoloration, excessive flash, or underfill 检查Powercore Front Plate（602-00001）产品的裂缝，凹痕，划伤，污点或者缺胶。
7 | Inspect light pipe installation for presence and proper seating 检查light pipe （602-00129）有安装并安装正确。
8 | Inspect sensor ring assembly to ensure that the parts are not snapped together 检查sensor ring assembly （800-00002）,确保产品都相互扣装好了.
9 | Make sure the sensor is correctly packaged in bubble bag with label that contains the part number and “made in china”
10 | Ensure box part number, quantity, and label matches the contents 确保纸浆盒产品编号,数量和标签要与实际物品一致.
11
12
13

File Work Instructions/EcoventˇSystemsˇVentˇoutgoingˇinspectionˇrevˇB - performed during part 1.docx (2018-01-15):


Ecovent Systems

Vent Outgoing Inspection Criteria

Vent组装件出货检验标准

Date and Time（日期和时间）: ____________________

Production Lot Number and Quantity（生产批号和数量）: ______________

Part Number（产品编号）: _____________________

Part Description and color产品描述及产品颜色: ______________________

Item | Inspection Step | Inspected By 检测员 | Quantity Passed 合格数量 | Quantity Failed 不合格数量
1 | Verify side screws are installed to torque of 40 +/- 4 in-oz and are fully seated to outer box 检查边端的螺丝有安装好，扭至40 +/- 4 in-oz，并且完全位于Outer box(NSM15196,NSM15201)产品内。
2 | Verify all magnets are installed and present in frames, outer boxes, faceplate covers, faceplate extensions, and floor faceplates
2 | Verify frame and faceplate cover are magnetically attached at all magnet points and all magnets and steel blocks are free of damage, discoloration, scratches, and dents. 检查Frame和faceplate cover产品的所有装磁铁的地方都装好了磁铁，所有的磁铁，方铁都没有损坏，污点，划伤和凹痕。
3 | Verify foam backing is installed and flush to the vent frame 检查泡棉板贴好了，并于Vent frame(面框)齐平。
4 | Verify doors are properly seated in the frame track, mating lead screw nuts are engaged in each door, and nut mushroom feature is fully installed through door
5 | Inspect all visible surfaces of plastics for damage, dents, scratches, marks, excessive flash, glue bloom,underfill, broken tabs, etc. 检查所有可看得到的外观表面，没有损坏，凹痕，划伤，标记，披锋，胶水圈记，缺胶等。
6 | Verify ball joint screw is tightened to 25 in-oz and constrains faceplate extension movement when held in installation orientation. The faceplate should be parallel to the frame before packaging.
7 | Inspect for presence of battery pack, ensure battery pack terminals are all present and fully seated with no damage 检查电池组的安装，确认电池组的端口都安装好并位于正确位置，没有损坏。
8 | Inspect vent for misalignment/bowing at mating edges and surfaces with sub assemblies and sub components 检查VENT产品的边部和表面要齐平，没有弯曲，及检查子组装件和子产品。
9 | Ensure pressure sensor cover is taped on to the outer box and the cable is not pinched. 确保Pressure Sensor Cover（NSM15238）产品捆好至OUTER BOX(NSM15196,NSM15201)产品上，且电线没有被挤压住。
10 | Inspect doors to make sure they are fully seated on nut and are in the open position during the final inspection. 检查包胶模产品，与NUT产品完全装配好，最终检查期间要处于打开的状态。
11 | Make sure the vent is properly seated in the cardboard pulp tray with poly bag and lid attached
12 | Ensure box part number, quantity, and label matches the contents 确保纸浆盒的产品编号，数量，标签要与实际物品一致。
13 | Ensure floor faceplate screws are installed to a torque of 40 +/- 4 in-oz and are fully seated to the outer box. 确认所有的floor faceplate(NSM15226产品)的螺丝都所扭至40 +/- 4 in-oz，并与OUTER BOX(NSM15196,15201)产品完全组装好。
14 | Ensure motor and sensor cables are visible in the battery compartment and not damaged. 确保马达和传感电线在电池盒里是可以看得到的，且没有损坏。
15 | Ensure that floor vents are made of black/brown plastic and wall and ceiling vents are made of white plastic. This includes battery pack, foam seal, and pressure sensor cover. 确保Floor vents(地面通风)的产品颜色全部是黑色/棕色的,wall,ceiling vents(墙面，天花板通风)组装件的颜色是白色的。包括电池组，泡棉板和传感器盖（NSM15238）产品都是这样。
16 | Ensure box full closes without pressure and that rubber band is around the center of the box. 要确保纸浆盒不需要施力就可以完全合盖好，大约在纸浆盒的中间用橡皮筋捆好。
17 | Ensure each vent box is right side up and properly seated in master carton. 确保每个VENT组装件的纸浆盒是正面朝上，并正确地放入运输外箱内。

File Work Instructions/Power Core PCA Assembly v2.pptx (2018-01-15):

## Power Core PCA Assembly Instructions Item Name: Power Core PCA Part number: 701-00012 Doc Revision: 2

## History Log

1) Revision 1 - Initial Release
2) Revision 2 – Clarified final location of the transformer wire to facilitate future assembly steps

## Take the new capacitor C3, 101-00028 rev B

Add 3 layers of tape,
103-00003 rev A

Bend the leads out as close to the cap body as possible

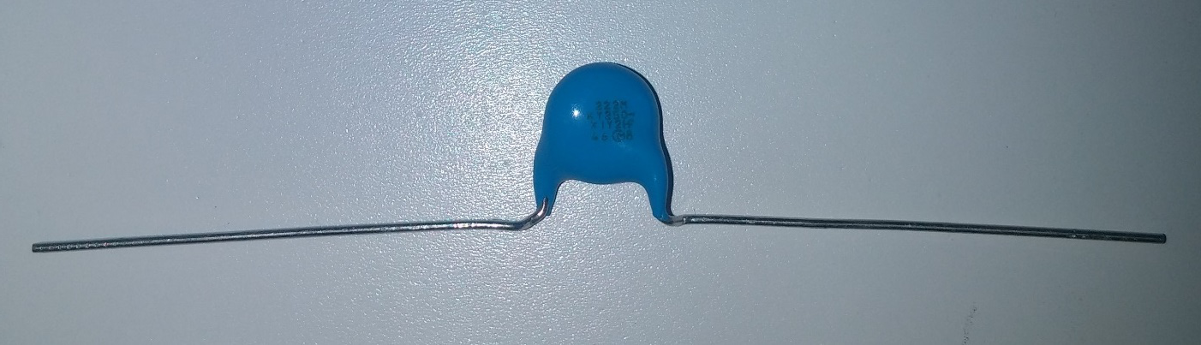
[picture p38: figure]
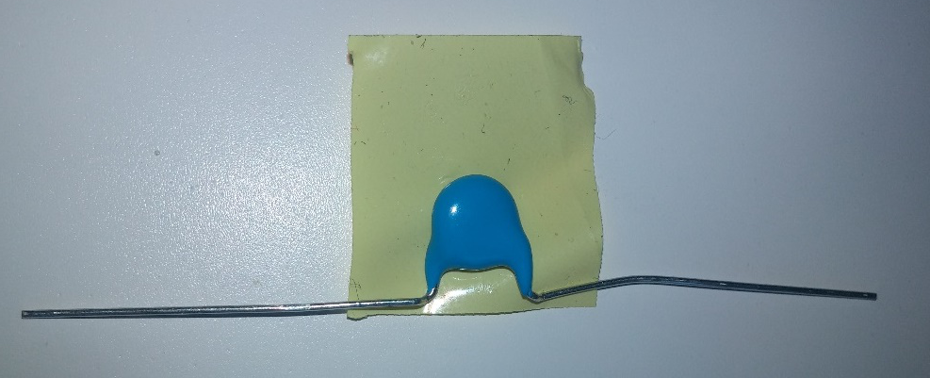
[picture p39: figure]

20 mm

18 mm

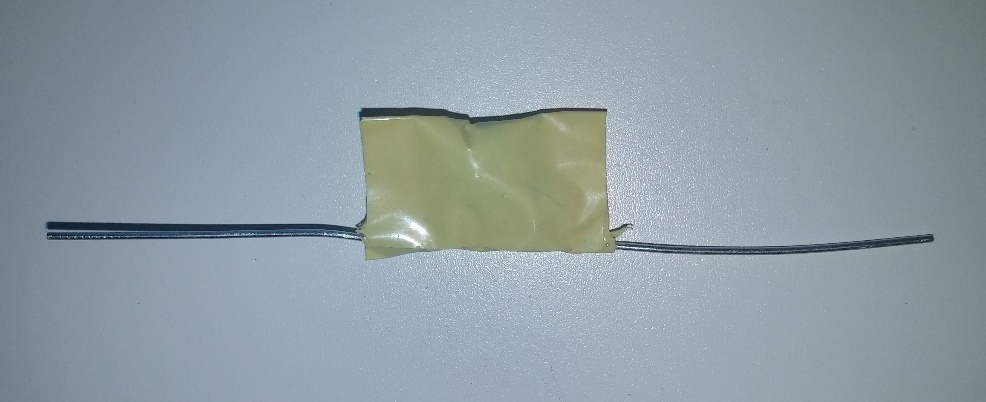
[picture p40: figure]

Note: AC mains wires are not shown in this presentation

## Take the Power Core Primary PCA, 701-00008 rev D

Precut the tape

Add 3 layers of tape,
103-00003 rev A

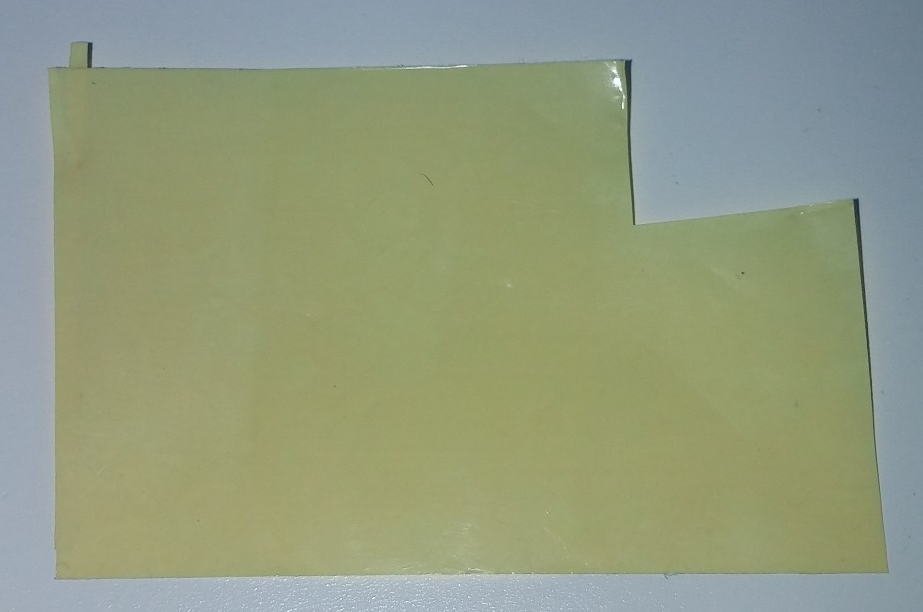
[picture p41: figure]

Non-adhesive side

30 mm

10 mm

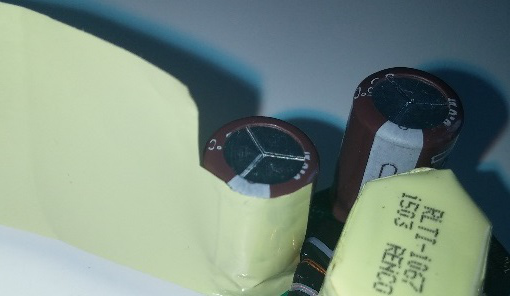
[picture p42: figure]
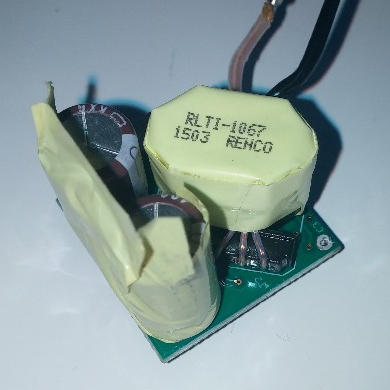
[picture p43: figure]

9 mm

25 mm

16 mm

Start between cap and transformer

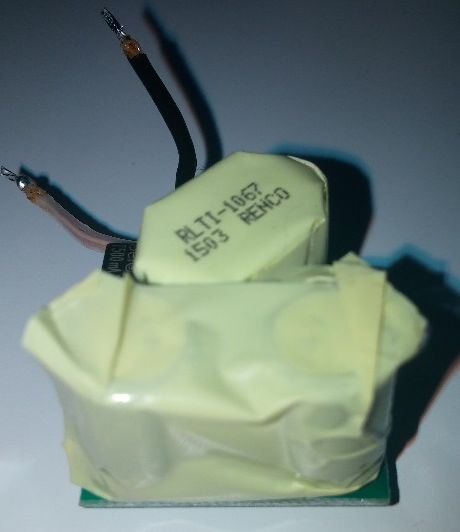
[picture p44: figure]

Cover the cap tops completely

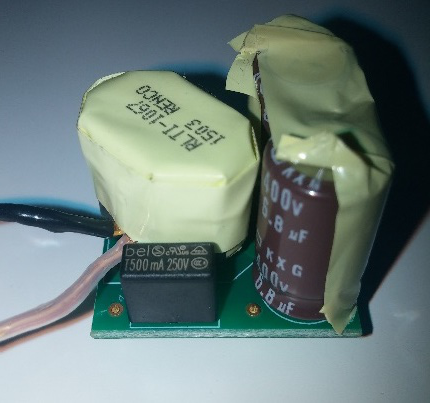
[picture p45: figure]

Keep this cap side uninsulated for easier fit in the housing

40 mm

Note: AC mains wires are not shown in this presentation

## Take the Power Core Secondary PCA, 701-00013 rev C

Solder transformer secondary leads to the secondary board

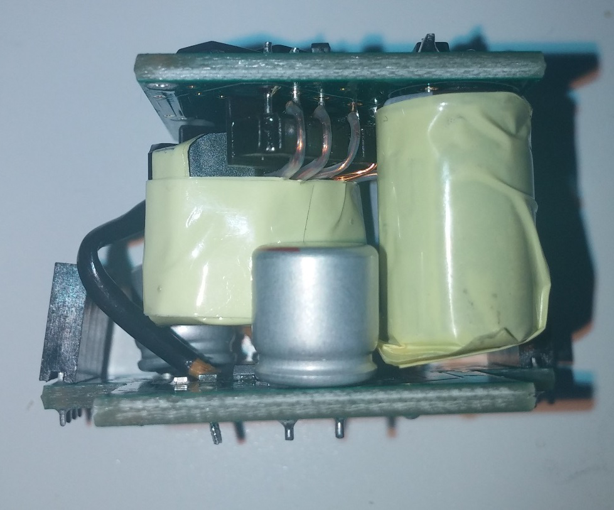
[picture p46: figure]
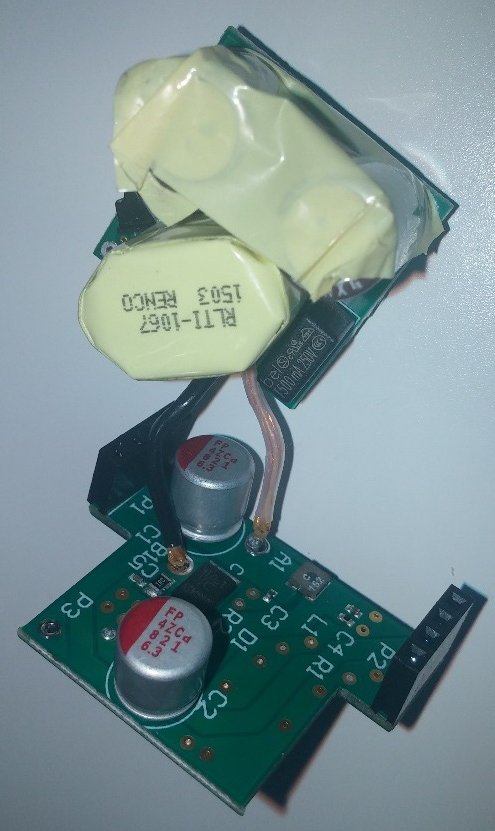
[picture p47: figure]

Note: AC mains wires are not shown in this presentation

## Place insulated capacitor C3, 101-00028 rev B

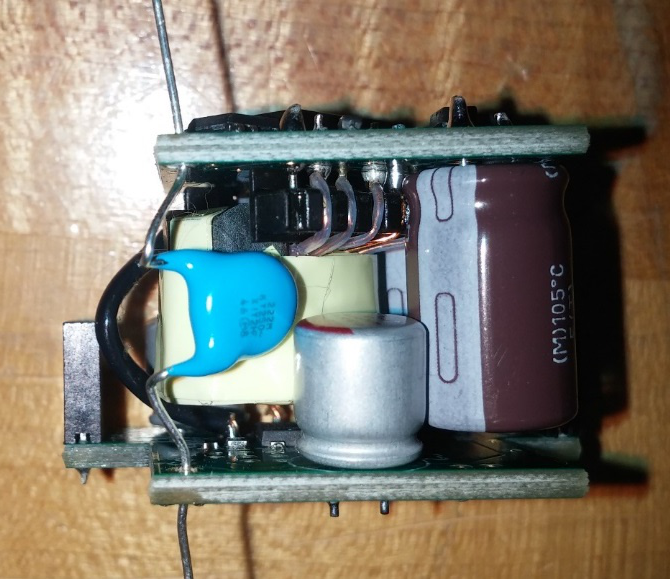
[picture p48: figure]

Uninsulated view

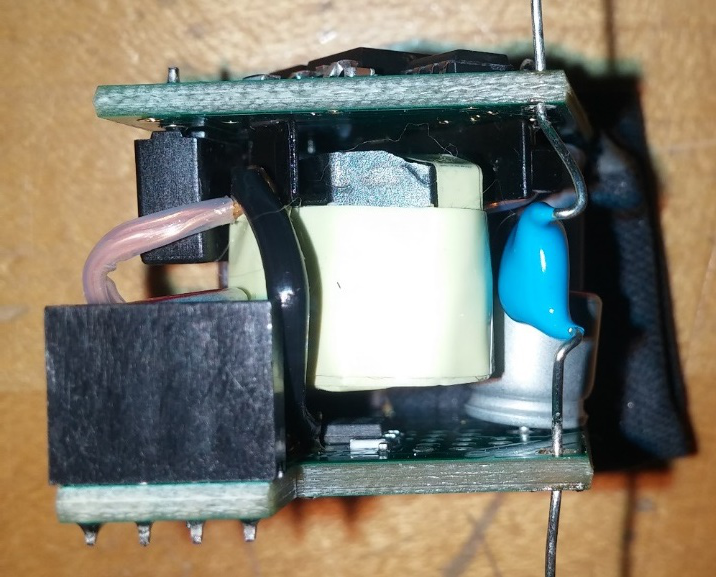
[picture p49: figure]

Uninsulated view

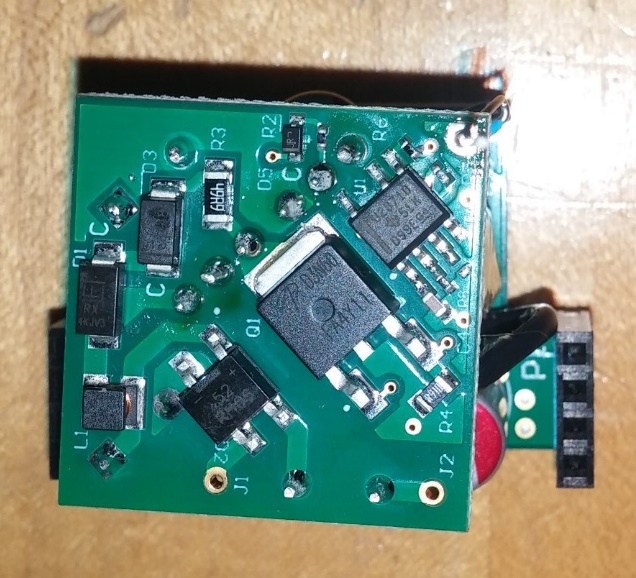
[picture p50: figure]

Uninsulated view

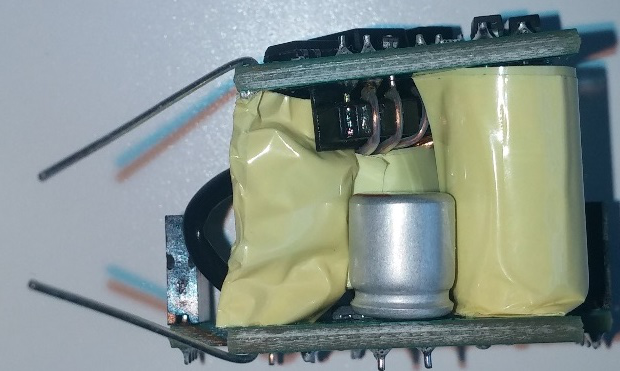
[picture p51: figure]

Insulated view

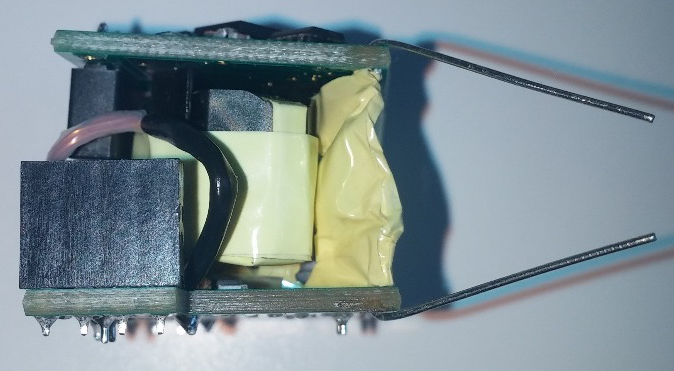
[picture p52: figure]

Insulated view

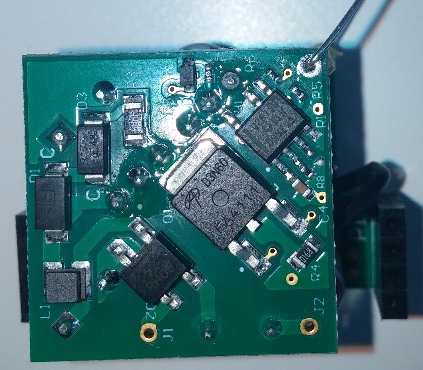
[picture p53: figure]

Insulated view

Orient the capacitor toward the middle of the power core, so that it doesn’t stick out

Note: AC mains wires are not shown in this presentation

## Solder and trim the capacitor C3 leads

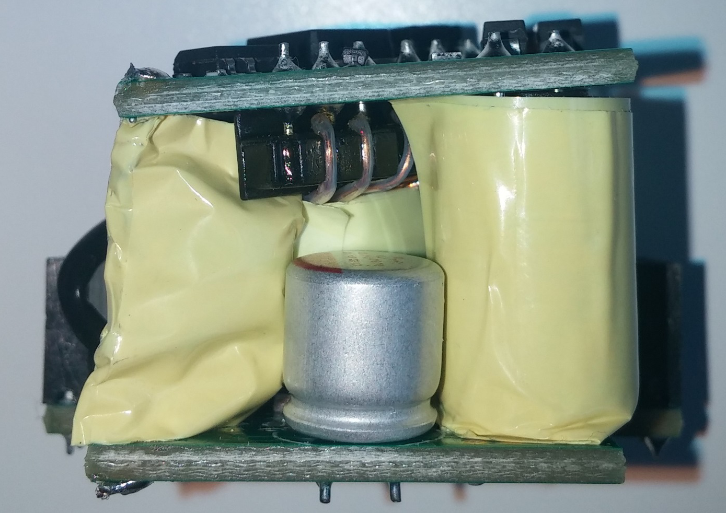
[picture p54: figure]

Note: AC mains wires are not shown in this presentation

## Move transformer secondary wire, B1, closer to the power core PCA body

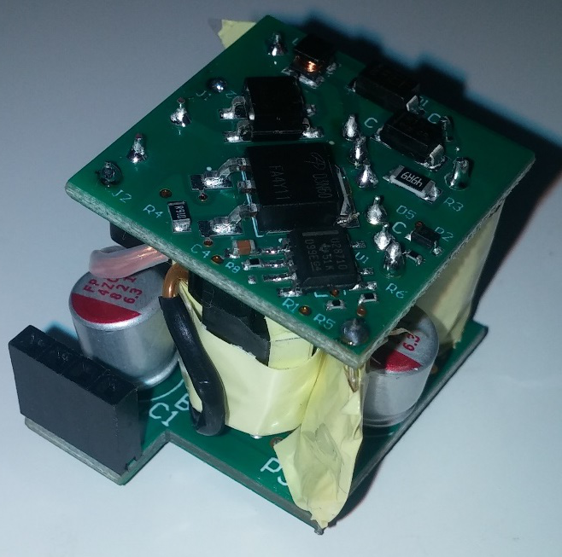
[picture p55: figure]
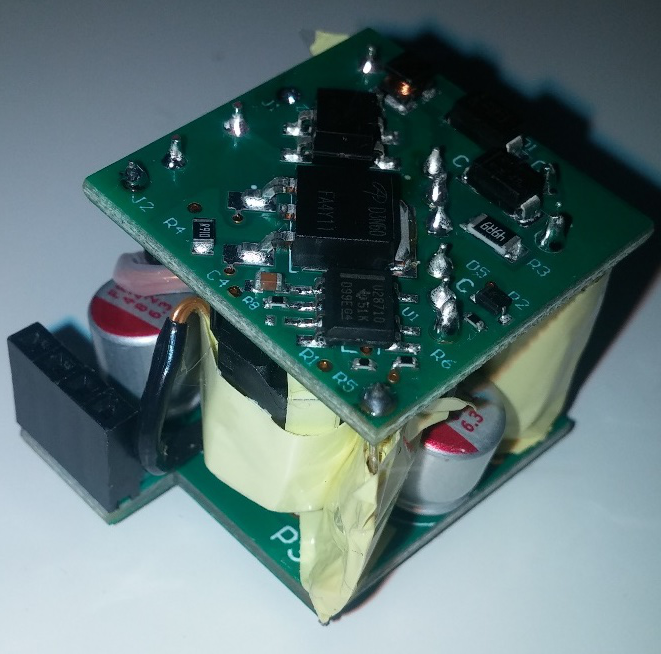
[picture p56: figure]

Good

Bad

Note: AC mains wires are not shown in this presentation

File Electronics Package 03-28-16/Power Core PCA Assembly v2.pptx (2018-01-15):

## Power Core PCA Assembly Instructions Item Name: Power Core PCA Part number: 701-00012 Doc Revision: 2

## History Log

1) Revision 1 - Initial Release
2) Revision 2 - Added a step to move the transformer wire closer to the body

## Take the new capacitor C3, 101-00028 rev B

Add 3 layers of tape,
103-00003 rev A

Bend the leads out as close to the cap body as possible


20 mm

18 mm


Note: AC mains wires are not shown in this presentation

## Take the Power Core Primary PCA, 701-00008 rev D

Precut the tape

Add 3 layers of tape,
103-00003 rev A


Non-adhesive side

30 mm

10 mm


9 mm

25 mm

16 mm

Start between cap and transformer


Cover the cap tops completely


Keep this cap side uninsulated for easier fit in the housing

40 mm

Note: AC mains wires are not shown in this presentation

## Take the Power Core Secondary PCA, 701-00013 rev C

Solder transformer secondary leads to the secondary board


Note: AC mains wires are not shown in this presentation

## Place insulated capacitor C3, 101-00028 rev B


Uninsulated view


Uninsulated view


Uninsulated view


Insulated view


Insulated view


Insulated view

Orient the capacitor toward the middle of the power core, so that it doesn’t stick out

Note: AC mains wires are not shown in this presentation

## Solder and trim the capacitor C3 leads


Note: AC mains wires are not shown in this presentation

## Move transformer secondary wire, B1, closer to the power core PCA body


Good

Bad

Note: AC mains wires are not shown in this presentation

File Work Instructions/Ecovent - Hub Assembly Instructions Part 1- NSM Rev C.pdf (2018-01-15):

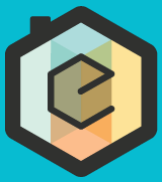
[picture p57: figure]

# Ecovent Hub Assembly Instructions

### Revision: C Issued: March 30th, 2016

# | Revision | Description of Change | Created By | Approved By | Effective Date

1 | - | Initial Release | M. DeLorenzo | M. DeLorenzo | 12/05/2015
2 | A | Added packing instruction, updated heat staking application methods | M. DeLorenzo | M. DeLorenzo | 01/25/2015
3 | B | Updates for changes 16.02 | A. Koukhtieva | T. Frey | 03/29/16
4 | C | Corrected Packaging Instructions | A. Koukhtieva | T. Frey | 03/30/16

# Ecovent Hub Assembly Instructions

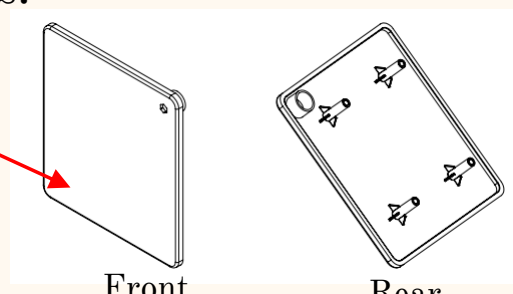
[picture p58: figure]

Front | Rear

# Ecovent Hub Assembly Instructions

1. Locate the following parts:
- Control Hub Top Plate
( PN 602-00033 ), qty. 1

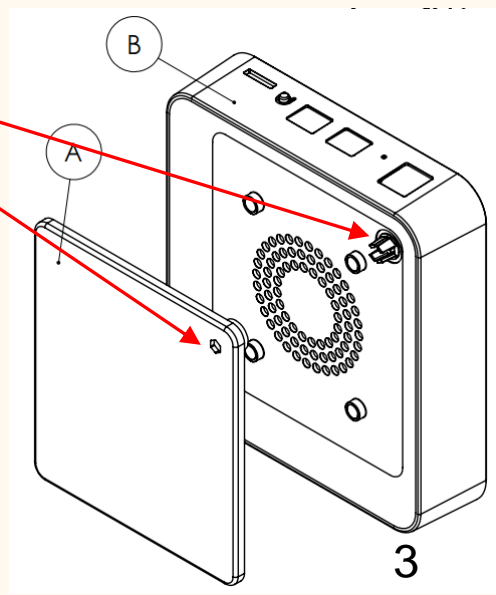
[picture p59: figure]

- Control Hub Main Housing ( PN 602-00032), qty. 1
- Control Hub Light Pipe
( PN 602-00131 ), qty 1

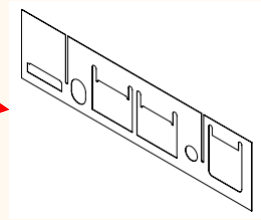
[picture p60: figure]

- Control Hub Foil
( PN 103-00001 ), qty. 1
2. Install the Control Hub Top Plate ( PN 602-00033 ) on to the Control Hub Main
Housing ( PN 602-00032) by aligning the Light Pipe
mounting features.

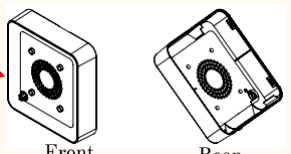
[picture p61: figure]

Front | Rear

# Ecovent Hub Assembly Instructions

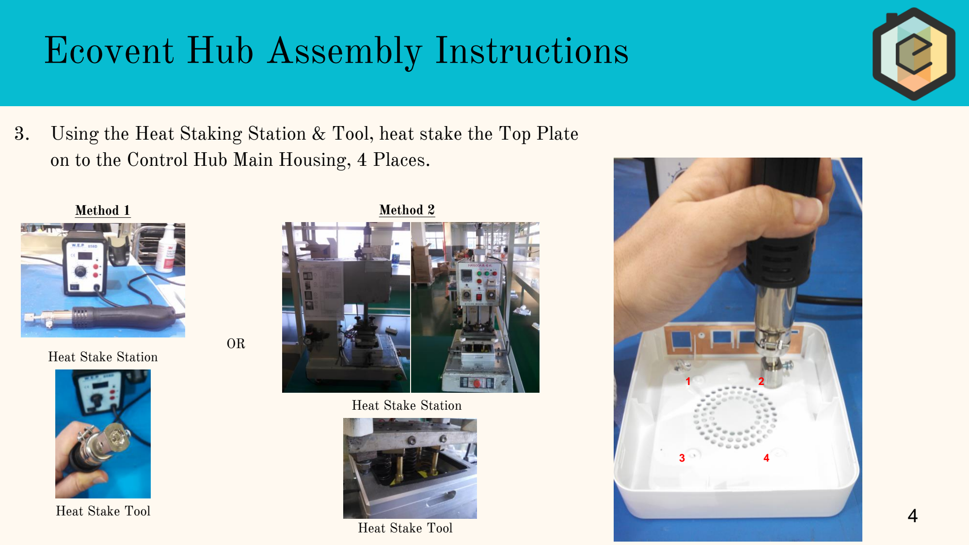
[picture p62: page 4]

3. Using the Heat Staking Station & Tool, heat stake the Top Plate on to the Control Hub Main Housing, 4 Places.

Heat Stake Station

Heat Stake Tool

1 2

3 4

OR

Method 1 | Method 2

Heat Stake Station

Heat Stake Tool

4. Remove the adhesive protective paper from the Control Hub Foil ( PN 103-00001 ). Place adhesive side of the Foil towards the Hub Plastic Housing. Align the rectangular cutouts in the Control Hub Foil with the Rectangular Connector cutouts in the Control Hub Main Housing PN 602-00032.

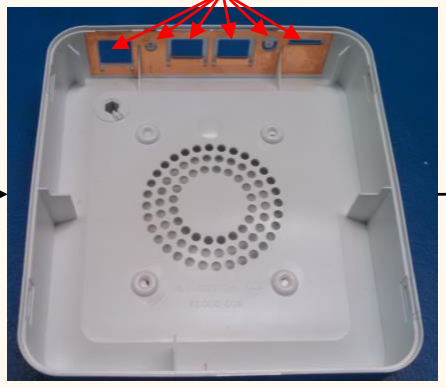
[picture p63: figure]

Control Hub Foil
( PN 103-00001 )

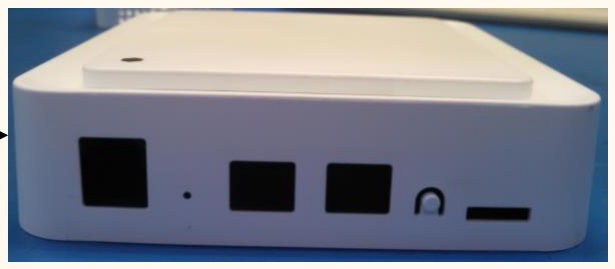
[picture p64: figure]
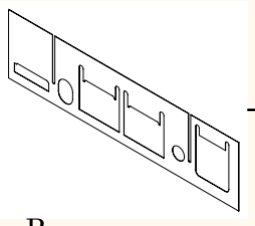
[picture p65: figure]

Remove paper
from adhesive side

Align cutouts in foil & housing,
6 places | Ensure Foil is not misaligned with
| cutouts in the Hub Housing

# Ecovent Hub Assembly Instructions

5. Install the Control Hub Light Pipe ( PN 602-00131 ), qty 1 into the Control Hub Main Housing ( PN 602-00032). Use the Light Pipe Alignment feature to determine the orientation. Gently press the light pipe until fully seated.

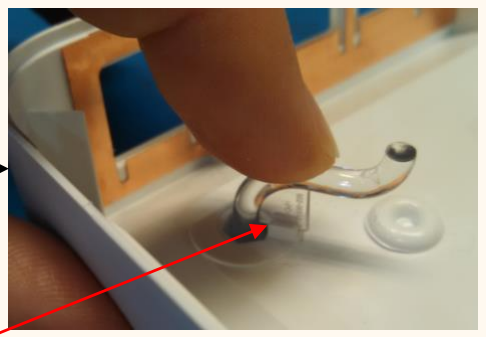
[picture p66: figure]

Control Hub Light Pipe
( PN 602-00131 )

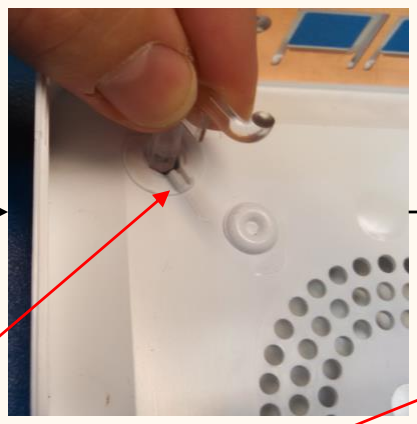
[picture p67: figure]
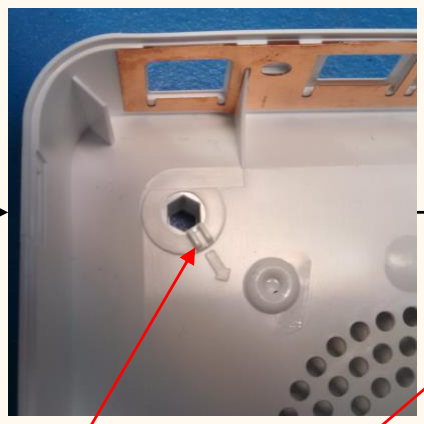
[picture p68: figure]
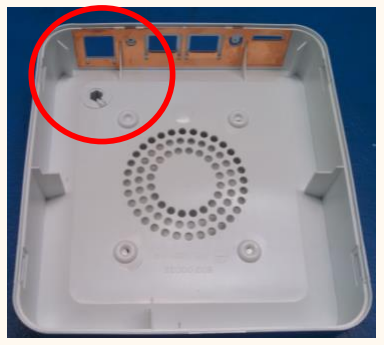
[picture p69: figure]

Note: Light Pipe Alignment Feature

# Ecovent Hub Assembly Instructions

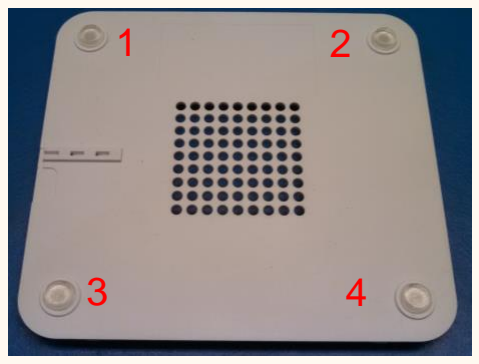
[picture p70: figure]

6. Locate the following parts:

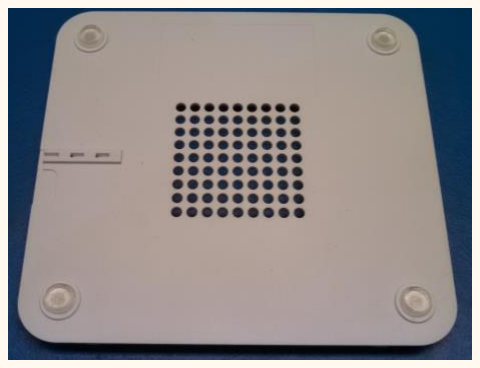
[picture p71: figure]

- Control Hub Bottom Plate
( PN 602-000331), qty. 1

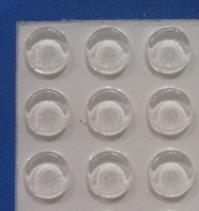
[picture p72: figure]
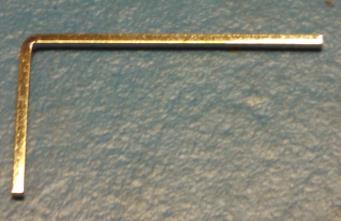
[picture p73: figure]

- Rubber Foot
( PN 603-00007), qty. 4
- Reset Button Push Tool
( PN 601-00015 ), qty. 1
7. Install the qty. 4 Rubber Feet onto the Control Hub Bottom Feet, 4 places

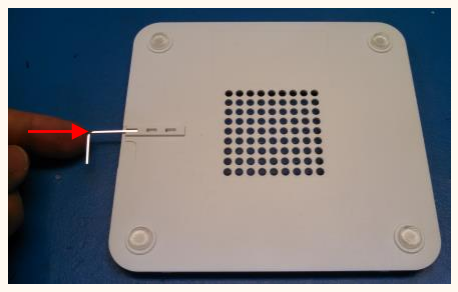
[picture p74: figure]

8. Install qty. 1 Reset Button Tool

# Ecovent Hub Assembly Instructions

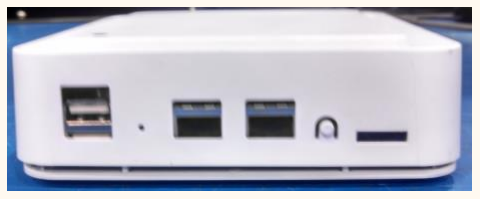
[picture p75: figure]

9. Join the Control Hub Top Plate with the Control Hub Main Housing. DO NOT SNAP TOGETHER.
10. Place inside Bubble Bag prior to Control Hub Bulk Packaging and label with part number and “made in china”.
11. Bulk pack pulp packaging (401-00027, 401-00028), rubber bands (401-00072), and small poly bags (401-00089)
12. In separate package, send M2.5x5 Button Head Plastite Screw, PN 603-00020 (4 Screws per Control Hub assembly).

# Ecovent Hub Assembly Instructions

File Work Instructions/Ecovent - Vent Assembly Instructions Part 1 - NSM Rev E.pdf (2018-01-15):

# Ecovent Vent Assembly Instructions

# Revision: E Issued: March 31th, 2016

# Ecovent Vent Assembly Instructions

# | Revision | Description of Change | Created By | Approved By | Effective Date

1 | - | Initial Release | M. DeLorenzo | M. DeLorenzo | 12/05/2015
2 | A | VA Assy for New Star | J. Pentecost | J. Pentecost | 12/07/2015
3 | B | Updates for GA | J. Pentecost | M. DeLorenzo | 01/25/2016
4 | C | Added Nylock Nut, Updated Vent Cover Shipping Instructions, Added Floor Vent Faceplate Installation Process | M. DeLorenzo | M. DeLorenzo | 02/18/2016
5 | D | Updated magnet installation instructions | T. Frey | T. Frey | 03/24/16
6 | E | Allow cleaning of hands with alcohol as alternative to wearing gloves | T. Frey | T. Frey | 03/31/16

# Ecovent Vent Assembly Instructions

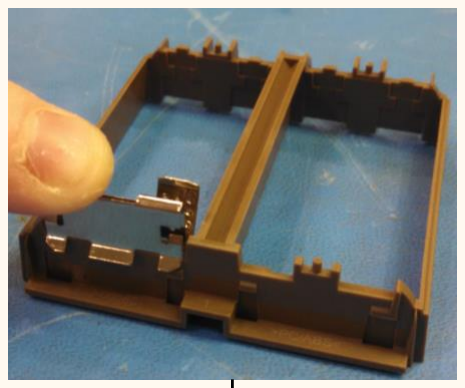
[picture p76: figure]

1. Snap Series Battery Connections, PN 601-00007,

## qty. 2 onto the Battery Pack Housing, PN 602-

00060, qty. 1 as shown.

## Battery Pack Assembly

Series Battery Connection
( PN 601-00007 ), qty. 2

Battery Pack Housing
( PN 602-00060-BRO ), qty. 1

Ensure Series Connections clip into Battery Pack Housing, 2 places.

1 | 2

# Ecovent Vent Assembly Instructions

Battery Pack Terminal ( PN 602-00014 ), qty. 2; Ensure the Battery Pack Terminal is fully seated in the housing; Note Negative spring location; Note Negative spring locations; Repeat 2; nd location

## 2. Install Battery Pack Terminal, PN 602-00014, onto the Battery Pack Housing

opposite negative spring.

## 3. Clip the Battery Spring Positive, PN 601-00016 over the Battery Pack Terminal. It

should make a ‘snap’ sound when finished.

## 4. Repeat Step 2 & 3 for the second location

## Battery Pack Assembly (continued)

Battery Spring Positive
( PN 601-00016 ), qty. 2

# Ecovent Vent Assembly Instructions

## 5. Install Battery Pack Terminal, PN 602-00014, onto the Battery Pack Housing

opposite positive spring.

## 6. Clip the Battery Spring Negative, PN 601-00010 over the Battery Pack Terminal. It

should make a ‘snap’ sound when finished.

## 7. Repeat Step 5 & 6 for the second location

## Battery Pack Assembly (continued)

Battery Spring Negative
( PN 601-00010 ), qty. 2

# Ecovent Vent Assembly Instructions


## 8. Install Battery Pack Ribs, PN 602-00144

onto Battery Pack Housing, 2 places.

## 9. Heat stake Battery Pack Ribs onto Battery Pack Housing, 4 places using the indicated

machine.

## 10. Visually inspect for proper appearance

## Battery Pack Assembly (continued)

Battery Pack Rib
( PN 602-000144-BRO ), qty. 2

# Ecovent Vent Assembly Instructions

1. Lightly sand flat face of Steel Block with 200-400 grit sandpaper.
2. Thoroughly clean hands with isopropyl alcohol. STEPS 3-5 MUST BE COMPLETED IN SUCCESSION.
3. Clean steel block with isopropyl alcohol
4. Clean application area with isopropyl alcohol
5. Ensure alcohol on steel block and application area is fully dry. Install qty. 4 Steel Blocks, PN 601-00017, into the Deflector Cover with sanded side towards plastic, using 2 drops Loctite 411, PN 604-00009, and dispensing tip for each location (4 places). Use press to ensure steel blocks are fully seated.
6. ALLOW 24 HOURS FULL CURE TIME BEFORE USING PART IN ANY OTHER ASSEMBLY

## Deflector Cover Steel Block Installation

Loctite 411
( PN 604-00009 )

Deflector Cover,
Steel Block | multiple PNs listed below
1/8 x 3/8 x 1/16
( PN 601-00017 )

# Ecovent Vent Assembly Instructions

1. Lightly sand SOUTH side of magnet with 200-400 grit sandpaper.
2. Thoroughly clean hands with isopropyl alcohol. STEPS 3-5 MUST BE COMPLETED IN SUCCESSION.
3. Clean magnet with isopropyl alcohol
4. Clean application area with isopropyl alcohol
5. Ensure alcohol on steel block and application area is fully dry. Install qty. 4 Magnets, PN 603-00006, into the Faceplate Extension with sanded side towards plastic, using 2 drops Loctite 411, PN 604-00009, and dispensing tip for each location (4 places). Use press to ensure magnets are fully seated.


6. ALLOW 24 HOURS FULL CURE TIME BEFORE USING PART IN ANY OTHER ASSEMBLY

## Faceplate Extension Magnet Installation

Magnet
3/8 x 1/8 x 1/16
( PN 603-00006 )

Loctite 411
( PN 604-00009 )

Faceplate Extension
Applies to multiple PNs,
see table below

# Ecovent Vent Assembly Instructions

## Vent Frame Magnet Installation

Frame
Applies to multiple PNs, see table below

Magnet
3/8 x 1/8 x 1/16
( PN 603-00006 )
1. Lightly sand NORTH side of magnet with 200-400 grit sandpaper.
2. Thoroughly clean hands with isopropyl alcohol. STEPS 3-5 MUST BE COMPLETED IN SUCCESSION.
3. Clean magnet with isopropyl alcohol
4. Clean application area with isopropyl alcohol
5. Ensure alcohol on steel block and application area is fully dry. Install qty. 4 Magnets, PN 603-00006, into the Frame with sanded side towards plastic, using 2 drops Loctite 411, PN 604-00009, and dispensing tip for each location (4 places). Use press to ensure magnets are fully seated.
6. ALLOW 24 HOURS FULL CURE TIME BEFORE USING PART IN ANY OTHER ASSEMBLY

Loctite 411
( PN 604-00009 )

# Ecovent Vent Assembly Instructions

## Outer Box Magnet Installation


Outer Box,
Applies to multiple
PNs, see table below

Magnet
3/8 x 1/8 x 1/16
( PN 603-00006 )
1. Lightly sand SOUTH side of magnet with 200-400 grit sandpaper.
2. Thoroughly clean hands with isopropyl alcohol. STEPS 3-5 MUST BE COMPLETED IN SUCCESSION.
3. Clean magnet with isopropyl alcohol
4. Clean application area with isopropyl alcohol
5. Ensure alcohol on steel block and application area is fully dry. Install qty. 4 Magnets, PN 603-00006, into the Outer Box with sanded side towards plastic, using 2 drops Loctite 411, PN 604-00009, and dispensing tip for each location (4 places). Use press to ensure magnets are fully seated.
6. ALLOW 24 HOURS FULL CURE TIME BEFORE USING PART IN ANY OTHER ASSEMBLY

Loctite 411
( PN 604-00009 )

# Ecovent Vent Assembly Instructions

## Floor Faceplate Magnet Installation

Floor Faceplate,
Applies to multiple
PNs, see table below

Magnet
3/8x1/8x1/16
( PN 603-00006 )
1. Lightly sand SOUTH side of magnet with 200-400 grit sandpaper.
2. Thoroughly clean hands with isopropyl alcohol. STEPS 3-5 MUST BE COMPLETED IN SUCCESSION.
3. Clean magnet with isopropyl alcohol
4. Clean application area with isopropyl alcohol
5. Ensure alcohol on steel block and application area is fully dry. Install qty. 4 Magnets, PN 603-00006, into the Floor Faceplate with sanded side towards plastic, using 2 drops Loctite 411, PN 604-00009, and dispensing tip for each location (4 places). Use press to ensure magnets are fully seated.
6. ALLOW 24 HOURS FULL CURE TIME BEFORE USING PART IN ANY OTHER ASSEMBLY

Loctite 411
( PN 604-00009 )

# Ecovent Vent Assembly Instructions

## Floor Faceplate Cover Steel Block Installation

1. Lightly sand flat side of Steel Block with 200-400 grit sandpaper.
2. Thoroughly clean hands with isopropyl alcohol. STEPS 3-5 MUST BE COMPLETED IN SUCCESSION.
3. Clean Steel Block with isopropyl alcohol
4. Clean application area with isopropyl alcohol
5. Ensure alcohol on steel block and application area is fully dry. Install qty. 4 Steel Blocks, PN 601-00017, into the Floor Faceplate Cover with sanded side towards plastic, using 2 drops Loctite 411, PN 604-00009, and dispensing tip for each location (4 places). Use press to ensure Steel Blocks are fully seated.
6. ALLOW 24 HOURS FULL CURE TIME BEFORE USING PART IN ANY OTHER ASSEMBLY


Loctite 411
( PN 604-00009 )

STEEL BLOCK
1/8 x 3/8 x 1/16
( PN 601-00017 )

Floor Faceplate Cover
(PN 602-00136)

# Ecovent Vent Assembly Instructions

### 1. Snap the Balljoint Faceplate Wall/Ceiling, PN 602-00076, into the Faceplate Extension. (Make sure that the magnets are already installed in the faceplate extension)

2. Snap the faceplate cover onto the assembly.

## Vent Assembly

Balljoint Faceplate
Wall/Ceiling
( PN 602-00076 )


Description | Extension Part Number | Assembly Part Number
10x6 Ceiling | 602-00091 | 801-00052
12x6 Ceiling | 602-00101 | 801-00058
10x4 Ceiling | 602-00111 | 801-00016
12x4 Ceiling | 602-00123 | 801-00014
10x4 Wall | 602-00137 | 801-00015
12x4 Wall | 602-00138 | 801-00013
10x6 Wall | 602-00139 | 801-00009
12x6 Wall | 602-00140 | 801-00064

See Faceplate Covers for
each assembly below

# Ecovent Vent Assembly Instructions

1. Install the Vent Seal onto the Outer Box.
Ensure all holes are aligned in the Seal and outer Box.

## Vent Assembly

Vent Seal | Set aside for later assembly Outer Box
Part Description | Vent Seal Part Number | Outer Box Part Number
10x6 White | 602-00089 | 602-00081 WHITE
12x6 White | 602-00095 | 602-00093 WHITE
10x4 White | 602-00105 | 602-00104 WHITE
12x4 White | 602-00116 | 602-00115 WHITE
10x6 Black | 602-00147 | 602-00081 BLACK
10x4 Black | 602-00148 | 602-00093 BLACK
12x4 Black | 602-00149 | 602-00104 BLACK
12x6 Black | 602-00150 | 602-00115 BLACK

# Ecovent Vent Assembly Instructions

## 1. Locate the following parts:

## Vent Assembly


Nut, Motor Side
( PN 602-00085 )

Nut, Bushing Side
( PN 602-00073 )

Diffuser Screw Cover

Lead Screw

Note: Bushing Side of
Lead Screw

Note: Motor Side of
Lead Screw
Description | Drive Train Assembly | Diffuser Screw Cover | Diffuser Screw Cover (Color) | Lead Screw
10x4 wall/ceiling | 801-00022 | 602-00107 | White | 602-00053
10x4 floor | 801-00027 | 602-00107 | Black | 602-00053
10x6 floor | 801-00028 | 602-00083 | Black | 602-00053
12x4 floor | 801-00029 | 602-00118 | Black | 602-00098
12x6 floor | 801-00030 | 602-00097 | Black | 602-00098
10x6 wall/ceiling | 801-00032 | 602-0008 | White | 602-00053
12x6 wall/ceiling | 801-00038 | 602-00097 | White | 602-00098
12x4 wall/ceiling | 801-00045 | 602-00118 | White | 602-00098

# Ecovent Vent Assembly Instructions

## 2. Install Lead Screw into the Diffuser Screw Cover

## 3. Ensure Bushing & Motor Side of the Diffuser Screw Cover matches the Bushing & Motor Sides of the Lead Screw

Note Bushing Side of the Diffuser Screw Cover has Pressure Sensor Wire Track in the Plastic

Busing side of Lead Screw


Slide the Lead Screw all the way through the Diffuser Screw Cover. Note the hole the screw must go through midway.

## Vent Assembly

# Ecovent Vent Assembly Instructions

## Vent Assembly

## 4. Thread the Cable, Vent Pressure Sensor, PN 801-00053 through the lower tunnel of the Diffuser Screw Cover from the Bushing End. See pictures showing the exit of

the Vent Pressure Sensor Cable.

Cable, Vent Pressure Sensor ( PN 801-00053 ), qty. 1

Note: The color of the
cable wires may be all black or multi-colored

# Ecovent Vent Assembly Instructions

## 5. Thread the Nuts, PNs 602-00073 and 602-00085, qty. 1 each onto the Lead

Screw.

## Note: PN 602-00073 is the Bushing Side Screw and PN 602-00085 is the Motor Side

Screw.


## Take care to thread the Nuts simultaneously so

that they start on the same screw thread.

Nut, Motor Side
( PN 602-00085 )

Nut, Bushing Side
( PN 602-00073 )

Rotate the Lead
Screw to thread Nuts
onto the Screw

Thread the Nuts all
the way to the middle
of the screw to check
alignment on the
screw. The nuts
should meet in the
enter at the same
time.

## Vent Assembly

# Ecovent Vent Assembly Instructions

## 6. Install Motor Cover Front, PN 602-00086

onto the Motor Stepper, PN 103-00045.

## Note the orientation. The grooved side of the Motor Cover Front mates flush with

the Motor.

## Place Rubber washers on screws


and insert screws into the motor.

## Vent Assembly

Motor Stepper
( PN 103-00045 )

Motor Cover Front
( PN 602-00086 )

Washer M3 Rubber
( PN 603-00004 )

Screw M3x8 Plastite
( PN 603-00005 )

Motor Cover Front
Grooved Side

# Ecovent Vent Assembly Instructions


## 7. Thread the motor power wires through the lower tunnel of the Diffuser Screw Cover. See pictures showing the exit of

the Motor Power Cable.

## Vent Assembly

Lower Tunnel


Motor Power Cable Exit Port in Diffuser Screw Cover

# Ecovent Vent Assembly Instructions

### 9. While in the Diffuser Screw Cover, rotate


### the Lead Screw until it mates with the Key

of the Motor Shaft.

## Vent Assembly

Motor Mount Standoffs on the Diffuser Screw Cover

8. Locate the Motor Mount Standoffs on the Diffuser Screw Cover. Torque the Screws, M3x8 Plastite, PN 603-00005, to 45 in-oz (+/− 4 in-oz) with T10 torx driver, 2 places. Torque must be verified and recorded during setup. Refer to torque setup instructions. If the screw begins to rotate freely before the torque setting is met, stop production and contact engineering.

Flat Keyed Surface of Motor Shaft

Internal feature in the Lead Screw is Keyed to Motor Shaft

Rotate Lead
Screw to
Seat on
Motor Shaft

# Ecovent Vent Assembly Instructions

10. Install Rubber Washers, PN 603-00004, qty. 4 and Screws M3x8, PN 603-00005, qty. 2 onto the Bushing PN 602-00055 as shown.

## Vent Assembly

Screw

Washer M3 Rubber
( PN 603-00004 ),
qty. 4

Screw M3x8 Plastite
( PN 603-00005 ),
qty. 2

Rubber Washer

Rubber Washer

Bushing | Bushing
( PN 602-00055 ),
qty. 1

# Ecovent Vent Assembly Instructions

11. Install the Bushing onto the Diffuser Screw Cover. Torque Screws to 40 in-oz (+/− 4 in-oz) with T10 torx driver, 2 Places. Torque must be verified during setup. Refer to torque setup instructions.
12. If the screw begins to rotate freely before the torque setting is met, stop production and contact engineering.

## Vent Assembly


## Note: ensure that pressure sensor wires are

inside routing tunnel.

## Note: lead screw should protrude past Bushing

# Ecovent Vent Assembly Instructions

### 13. Install the Locknut M2 Hex Stainless Steel, PN 603-00018, and Screw M2x10, PN 603-00014

into the Diffuser Screw Cover.

### Loosely Tighten the Screw onto the Nut. Ensure

the Motor Cable is routed underneath the screw.

## Vent Assembly

Screw M2x10 BH
Machine
( PN 603-00014 ), qty. 1

Locknut M2 Hex Stainless
Steel
( PN 603-00018 ), qty. 1


View from Nut Side
Note hexagonal cutout for Nut

Wall & Ceiling Vents Only

# Ecovent Vent Assembly Instructions

14. Pass the Motor Cable and Pressure Sensor Cable through the Balljoint Faceplate Wall/Ceiling &
15. Snap the ball joint into place on the diffuser screw cover.
16. Torque the screw to 25 in-oz (+/- 5 in-oz) using #1

Balljoint Faceplate Wall/Ceiling & Faceplate Extension Assembly

After the ball joint components have snapped

Sensor Cable here. Battery PCBA will not

# Ecovent Vent Assembly Instructions


## 17. Install the Flexible Doors into the Outer Box. Snap Balls at either end of the door

into the track on the Outer Box.

## Vent Assembly

Insert the door into the track and feed it in, ensuring all of the balls are in the track

Part Description | Door Part Number | Outer Box Part Number
10x6 White | 602-00088 WHITE | 602-00081 WHITE
12x6 White | 602-00113 WHITE | 602-00093 WHITE
10x4 White | 602-00114 WHITE | 602-00104 WHITE
12x4 White | 602-00121 WHITE | 602-00115 WHITE
10x6 Black | 602-00088 BLACK | 602-00081 BLACK
10x4 Black | 602-00113 BLACK | 602-00093 BLACK
12x4 Black | 602-00114 BLACK | 602-00104 BLACK
12x6 Black | 602-00121 BLACK | 602-00115 BLACK

Inspect the assembly to make sure the snap features are in the center and all balls are located in the track

# Ecovent Vent Assembly Instructions

18. Thread the Pressure Sensor Cable through the Outer Box Cable Way Pull through until Driveshaft edge and Outer Box are in contact.; Vent Assembly; Pressure Sensor; Cable Way; 19. Move the Drive Train Assembly into the Outer Box. Take care not to damage the Pressure Sensor Cable. The Diffuser Screw Cover should

seat flush with the Outer Box.

Surfaces must be flush all the way around

# Ecovent Vent Assembly Instructions


## 20. Snap the Motor & Bushing Nuts onto the

Flexible Doors.

## First, insert the Toe into the Nut Mounting

feature and then snap in the heel of the Nut.

Repeat this operation for both doors.

## Vent Assembly

Snap Nut Toe into the Door Mounting Feature

Snap Nut Heel into the
Door Mounting Feature

# Ecovent Vent Assembly Instructions

## Vent Assembly

## From the back side of the vent, make sure the Nut Mushroom is properly installed into the

Flexible Door.

## Fold door material around the mushroom feature

using flathead screwdriver.

Vent is ready for mechanical test. | 29

Nut “Mushroom” feature

### Examples of Correctly Installed Nut “Mushroom” features

### Examples of Incorrectly Installed Nut “Mushroom” features

Door TPE IS NOT flat around mushroom

Door TPE IS flat around mushroom

# Ecovent Vent Assembly Instructions

21. Install the side screws PN 603-00019 into the vent. (8 locations, 4 each side). Inspect to ensure that the screw head is fully seated.


## Ensure that the screw bosses are aligned with the thru holes in the

outer box.

## Install the screws to the specified torque of 40 in-oz (+/- 4 in-oz) with

T8 torx driver.

## Note: If the screw begins to rotate freely before the torque setting is

met, stop production and contact engineering.

## 22. Mechanically Test the Vent according to the procedure

provided. Record all results according to the Test Procedure.

## Vent Assembly

23. Pass the Motor Cable and Pressure Sensor Cable through the Faceplate Floor. Part Numbers provided below. Note the orientation of the drivetrain Balljoint feature to the feature in
24. Install PN 603-00017 - Screw #6-19x1/4" Thread Forming for Plastic, Qty. 4. Torque to 40 in-oz (+/- 4 in-oz) using T10

Qty. 4. Torque to 40 in-oz (+/- 4 in-oz)

# Ecovent Vent Assembly Instructions

### 25. Place the PCA Cover, PN 602-00078, into the balljoint extension. This will be placed

loose on the battery pack side of the assembly. See figures to the right.

## Vent Assembly

Vent PCB Cover
( PN 602-00078 ), qty. 1
Wall & Ceiling Vents - Only | Floor Vents - Only


Place Vent PCBA Cover loose in these locations.

# Ecovent Vent Assembly Instructions

Vent PCBA Cover will actually be placed loose in these locations. See previous page.

26. Install Vent Frame and Faceplate Cover.

### The magnetic force will hold these parts onto

the vent.

## Vent Assembly

Install Faceplate Cover – All Vent Types

Wall & Ceiling Vents Only

# Ecovent Vent Assembly Instructions

## Vent Assembly

Vent Pressure Sensor Cover, qty. 1

10 inch
( PN 602-00082 )

12 inch
( PN 602-00094 )
27. Place the Vent Pressure Sensor Cover, PN 602-00082, onto the Outer Box.

## Apply Tape, PN 604-00005 (Scotch Film Strapping Tape 8898), to hold the cover in

place during shipment.

Vent is ready for packaging.


Apply Tape, 2 Places.

# Ecovent Vent Assembly Instructions

## Vent Packaging

1. Place the Battery Pack in the Vent Molded Pulp – Bottom.
2. Place the Battery Pack Foam over the Battery Pack and press into the space in the Molded Pulp – Bottom

Vent Molded Pulp – Exterior

Vent Molded Pulp – Interior

Vent Molded Pulp – Exterior

Vent Molded Pulp – Interior | Note shape of the battery pack
3. Place the Vent in the Vent Molded
| Pulp – Bottom.
4. Place the vent foam into the Molded Pulp – Top. Make sure it is fully pressed into the packaging.
TOP | BOTTOM

# Ecovent Vent Assembly Instructions

## Vent Packaging


5. Place the Molded Pulp – Top with foam onto the Molded Pulp – Bottom with Vent.
6. Apply quantity 2, Rubber Bands, as shown.

Vent is Ready for Shipment. Pack 12 Vents to a Master Carton.

Pack this side up in the Master Carton.

Place vent part number & size label here

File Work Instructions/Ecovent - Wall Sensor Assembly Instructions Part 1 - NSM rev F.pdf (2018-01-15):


# Ecovent Wall Sensor Assembly Instructions

### Revision: F Issued: March 30th, 2016

# Ecovent Wall Sensor Assembly Instructions

# | Revision | Description of Change | Created By | Approved By | Effective Date

1 | - | Initial Release | M. DeLorenzo | M. DeLorenzo | 11/25/2015
2 | A | Added Test Detail | M. DeLorenzo | M. DeLorenzo | 11/30/2015
3 | B | Added Powercore Instructions | M. DeLorenzo | M. DeLorenzo | 12/05/2015
4 | C | VA assy for New Star | J. Pentecost | J. Pentecost | 12/07/2015
5 | D | Added packaging instruction, updated torque to 5 in-lbs from 3 in-lbs | M. DeLorenzo | M. DeLorenzo | 01/25/2016
6 | E | Updated torque to in-oz units, new packaging instructions | A. Koukhtieva | T. Frey | 03/29/2016
7 | F | Corrected Packaging Instructions | A. Koukhtieva | T. Frey | 03/30/16

# Ecovent Wall Sensor Assembly Instructions

1. Locate the following
parts:
- Powercore Back Plate
( PN 602-00002 ),
qty. 1
- Powercore Hot Side
( PN 801-00003),
qty. 1
- Powercore Neutral Side
( PN 801-00004),
qty. 1
- Powercore Ground Assembly ( PN 801-00005), qty. 1


- Powercore Front Plate
( PN 602-00001 ), qty. 1


Exterior View Interior View

Wall Sensor Powercore Assembly

Top View

Side View

PN 801-00004 | PN 801-00003

# Ecovent Wall Sensor Assembly Instructions


2. Install PNs 801-00003 & 801-00004, Powercore Hot & Neutral bus bars, into the Powercore Back Plate housing. Place plugs through the rectangular holes in the housing plastic. Gently press the bus bars until they are flush with the plastic housing. Install two screws in the lower holes as shown. Installation torque must be 80 in-oz (+/- 4 in-oz).

Wall Sensor Powercore Assembly

Side View of fully seated
Hot & Neutral bus bars

Screw M2.5x6 Plastite
( PN 603-00001 ), qty. 2

Powercore Neutral Side
PN 801-00004

Powercore Hot Side
PN 801-00003

# Ecovent Wall Sensor Assembly Instructions

3. Install the Powercore Ground Assembled, PN 801-00005, into the Powercore Back Plate Housing. Position the Ground Prong into the round hole. Gently press using a wooden stick until the ground prong is fully seated. Install Screw M2.5x6 Plastite ( PN 603-00001 ), qty. 1 to attach the Powercore Ground. Torque to 80 in-oz (+/- 4 in-oz).

Wall Sensor Powercore Assembly


Powercore Ground Assembled ( PN 801-00005 ), qty. 1

Screw M2.5x6 Plastite
( PN 603-00001 ), qty. 1


Push Ground Prong into housing until fully seated
(PCBA shown for reference only)


Install one screw 603-00001 in the area shown. Torque to 80 in-oz (+/- 4 in-oz)

# Ecovent Wall Sensor Assembly Instructions

4. Install Powercore Assembly Tabs, PN 602-00003, qty. 3 into the Powercore Back Plate Housing. Gently press the Powercore Assembly Tabs until they snap into position. They will seat flush with the Powercore Back Plate Housing. Ensure each tab can rotate freely.

Wall Sensor Powercore Assembly


Powercore Assembly Tabs
( PN 602-00003 ), qty. 3

# Ecovent Wall Sensor Assembly Instructions

5. Mate Powercore housing assembly with Powercore faceplate and set aside to be paired with a Wall Sensor Ring Assembly for shipment.

Wall Sensor Powercore Assembly

Powercore Front Plate
( PN 602-00001 ), qty. 1

Exterior Side

Interior Side


***Note Orientation of plug and plug features on the Powercore Front Plate

# Ecovent Wall Sensor Assembly Instructions


1. Locate the following parts:
- Wall Sensor Ring Front
(PN 602-00005 ), qty. 1


- Wall Sensor Light Pipe
(PN 602-00129), qty. 1
2. Install Wall Sensor Light Pipe ( PN 602-00129) into the Wall Sensor Ring Front ( PN 602-00005 ) by placing the Light Pipe Exterior surface into the Light Pipe Hole in the Wall Sensor Housing.


Top View | Side View

+

Wall Sensor Ring Assembly

# Ecovent Wall Sensor Assembly Instructions

3. Gently press the rear of the Wall Sensor Light Pipe until the clips snap into place with Wall Sensor Housing mating feature.

Pictured below, completely installed Wall Sensor Light Pipe


Apply pressure in the
direction of the arrow,
the part will snap into


place | ***Note clip locations are attached over mounting feature, 2 places


Top View | Front View

Wall Sensor Ring Assembly

# Ecovent Wall Sensor Assembly Instructions

4. Place PN 602-00004, Wall Sensor Ring Back, on top of PN 602-00005, Wall Sensor Ring Front. DO NOT SNAP the two pieces together. Set aside for matching with the Powercore Assembly.

Wall Sensor Ring Assembly


PN 602-00004
Wall Sensor Ring Back


# Ecovent Wall Sensor Assembly Instructions

1. Place the Wall Sensor Ring Assembly onto the Powercore assembly, as shown. Place the Powercore Front Plate PN 602-00001, onto the assembly and secure with a Rubber Band.

Final Assembly and Shipment

Assembly is complete. Send Unit to Packaging

# Ecovent Wall Sensor Assembly Instructions

1. Place inside Bubble Bag prior to Wall Sensors bulk packaging and label with part number and “made in china”.
2. Bulk pack pulp packaging (401-00025, 401-00026), rubber bands (401-00072), and small poly bags (401-00089)
3. In separate package, send M2.5x6 Button Head Plastite Screws, PN 603-00001 (3 screws per Wall Sensor assembly).

Final Assembly and Shipment

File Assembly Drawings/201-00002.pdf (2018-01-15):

(COLORED WIRES); DETAIL E; SCALE 1 : 1; PRESSURE SENSOR WIRE ORIENTATION; INSERT BATTERIES AS SHOWN, 4 PLACES; APPLY ARROW; STICKER TO BALLJOINT INSTALLED VENT BOARD ORIENTATION.; FACEPLATE, 1 PLACE NOTE RESET BUTTON LOCATION.; DRAWING NO. 201-00002

TORQUE M2 BALLJOINT SCREW
TO SPECIFIED TORQUE

ASSEMBLED BATTTERY
PACK AND HARDWARE
SHIPPED ALONGSIDE
ASSEMBLED VENT.
DO NOT INSTALL.

GENERAL NOTES
1. SEE ARENA PLM FOR PART NUMBER REFERENCE
DESIGNATORS AND CURRENT REVISIONS.
2. [ ] CALLOUTS ARE APPLIED TO TOLERANCES THAT MAY
REQUIRE SPECIAL QUALITY CONTROL PROCESSES.
QUALITY CONTROL INSTRUCTIONS ARE OUTSIDE THE
SCOPE OF THIS DRAWING AND ARE DEFINED BY EXTERNAL
DOCUMENTATION TO BE AGREED TO WITH THE
MANUFACTURER.
3. ALL DIMENSIONS AND TOLERANCES MUST BE HELD
REGARDLESS OF THE USE OF QUALITY CONTROL SYMBOLS
4. ( X.XX ) DIMENSIONS ARE USED AS REFERENCE ONLY AND
ARE NOT SUBJECT TO TOLERANCES.
5. UNLESS OTHERWISE SPECIFIED, ALL DIMENSIONS AND
TOLERANCES ARE APPLICABLE AT 20 DEGREES CELCIUS
(68 DEGREES FAHRENHEIT) IN ACCORDANCE WITH
ANSI/ASME B89.6.2
6. ALL HOMOGENOUS MATERIALS AND PROCESSES IN THIS
DRAWING SHALL BE COMPLIANT TO THE EU RoHS
DIRECTIVE 2011/65/EC
7. REFER TO DETAILED WORK INSTRUCTIONS FOR ASSEMBLY
SPECIFICATIONS SUCH AS SCREW TORQUE AND GLUE
VOLUME.

VENT ID LABEL
APPLIED HERE,
NOTE ORIENTATION

MOUNTING POSITION OF
PRESSURE SENSOR

CORRECT POSITIONING OF VENT PCB,
POWER PCB, AND WIRES.

ENSURE WIRES ARE
BENEATH BATTERY BOARD

ASSEMBLY OVERVIEW:
(FOR REFERENCE ONLY. REFER TO DETAILED WORK INSTRUCTIONS FOR
PRODUCTION ASSEMBLY INSTRUCTIONS)
1. REMOVE THE MAGNETIC FACEPLATE COVER.
2. REMOVE THE VENT BOARD COVER FROM THE BALLJOINT FACEPLATE.
3. ATTACH THE BATTERY POWER CABLE TO THE BATTERY PCA.
4. INSERT THE BATTERY PCA AS SHOWN. ENSURE SNAPS ARE FULLY
ENGAGED. ENSURE WIRES ARE ROUTED BENEATH THE BOARD AS
SHOWN.
5. CONNECT THE THREE CABLE HARNESSES TO THE VENT BOARD AS
SHOWN. ENSURE THE MOLEX CONNECTORS ARE FULLY SEATED.
6. PLACE THE VENT BOARD INTO POSITION AND SNAP THE VENT BOARD
COVER ON TOP OF IT. ENSURE THE WIRES ARE NOT TANGLED OR
DAMAGED, AND ARE HIDDEN UNDER THE BOARD.
7. REMOVE TAPE AND REMOVE THE PRESSURE SENSOR COVER.
8. ATTACH THE PRESSURE SENSOR BOARD TO THE PRESSURE SENSOR
CABLE HARNESS. SEAT THE PRESSURE SENSOR IN POSITION ON THE
MAIN BODY AS SHOWN.
9. USE SCREWS TO ATTACH THE PRESSURE SENSOR COVER TO THE MAIN
BODY WHERE SHOWN.
10. APPLY 1 VENT ID LABEL CENTERED ON THE VENT BOARD COVER.
ENSURE THAT THE NOTCHED EDGE IS ORIENTED AWAY FROM THE
BATTERY PACK.
11. APPLY 1 VENT ID LABEL ONTO THE MAIN BODY AS SHOWN. ENSURE
THE NOTCHED EDGE IS ALIGNED WITH THE CUTOUT.
12. INSERT THE 4 BATTERIES INTO THE BATTERY PACK. USE THE POLARITY
INDICATORS ON THE BATTERY PACK TO ENSURE CORRECT POLARITY.
13. APPLY 2 ARROW STICKERS TO THE BATTERY PACK AS SHOWN.
14. APPLY 1 ARROW STICKER TO THE BALLJOINT FACEPLATE AS SHOWN.
15. REMOVE THE MAGNETIC FRAME.
16. TORQUE THE M2 BALLJOINT SCREW TO TORQUE SPECIFIED IN THE
DETAILED WORK INSTRUCTIONS.
17. RE-ATTACH THE MAGNETIC FRAME.
18. RE-ATTACH THE MAGNETIC FACEPLATE COVER.
19. BAG THE #8X2 SCREWS AND #8 WASHERS AS SHOWN IN DETAILED
WORK INSTRUCTIONS.
20. THE ASSEMBLED BATTERY PACK AND BAGGED HARDWARE ARE
SHIPPED ALONGSIDE THE VENT. DO NOT INSTALL THESE ITEMS.

MOLEX ON THIS SIDE
OF BATTERY BOARD

APPLY ARROW
STICKER TO BATTERY
PACK HERE, AND ON
MIRRORED FACE.
2 PLACES

VENT BOARD CONNECTIONS

REV | DESCRIPTION | ECO | DATE | BY | DO NOT SCALE DRAWING. WORK TO DIMENSION IF PLATING IS SPECIFIED, ALL DIMENSIONS TO BE MET AFTER PLATING UNLESS OTHERWISE SPECIFIED. DIMENSIONS= 0.015 1. PERMISSIBLE TOLERANCES ANGLES= 0.5 2. ALL RIGHT ANGLES=90 CHAMFER ANGLES= 5 3. DIMENSIONS GIVEN IN INCHES CONCENTRICITY=0.010 T.I.R.
A | INITIAL RELEASE (FROM 901-00002 DRAWING) | 000082 | 2/26/16 | AK
B | PART NUMBER AND DRAWING NUMBER UPDATE | DCO-000043 | 3/25/16 | AK
C | PART NUMBER AND DRAWING NUMBER UPDATE | DCO-000044 | 3/29/16 | AK

(BLACK WIRE, 4 PINS)

NOTICE: CHANGES TO MATERIAL, DESIGN, CONFIGURATION OR PROCESS MAY NOT BE MADE WITHOUT NOTIFICATION TO ECOVENT. ALL MATERIALS AND PROCESSES MUST BE COMPLIANT WITH ENVIRONMENTAL LAWS AND REULATIONS AS REFERENCED IN XXXXX | | CTQ | CLASSIFICATION OF CHARACTERISTIS DESIGN

APPLY VENT ID LABEL HERE,
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

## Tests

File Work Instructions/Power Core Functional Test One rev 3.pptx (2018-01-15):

## Functional Test 1 Item Name: Power Core Part number: 801-00001 Doc Revision: 3

## History Log

1. Revision 1 – Initial Release
2. Revision 2 – Minor Changes
3. Revision 3 – Add clarification for inspection step

## Tools

- AC power and ground tester
- 5V tester (multimeter + modified test cables)

## Make sure that the wires and brass are secure by lightly pushing on the components secured by the screws

## Make sure that the brass looks symmetrical

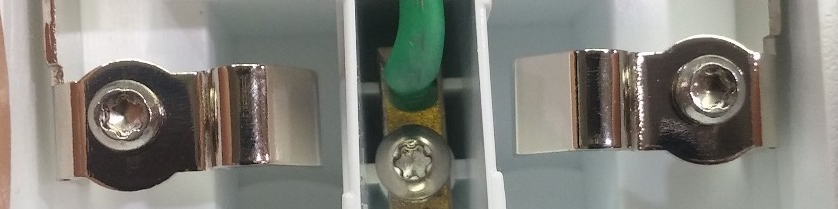
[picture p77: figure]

Good

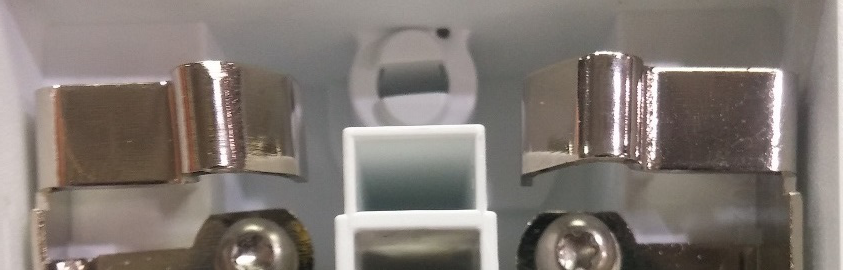
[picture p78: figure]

Good

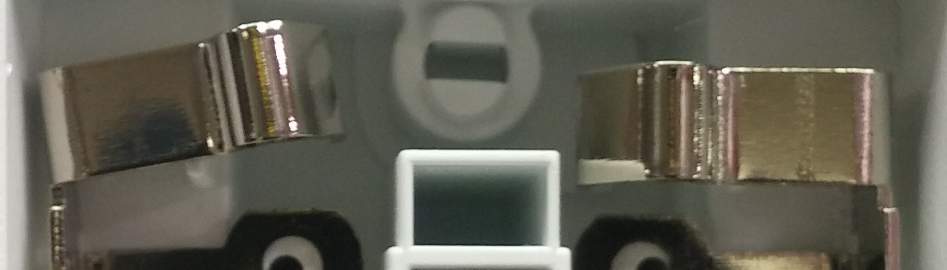
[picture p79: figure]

Bad

## Make sure that the ground is seated on top of the plastic

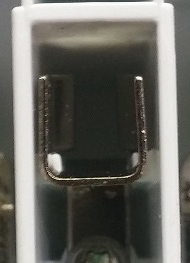
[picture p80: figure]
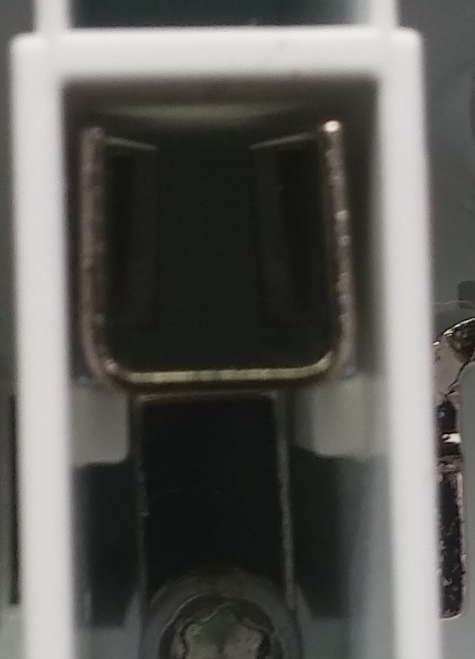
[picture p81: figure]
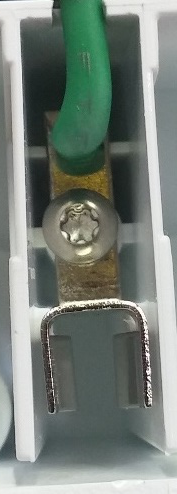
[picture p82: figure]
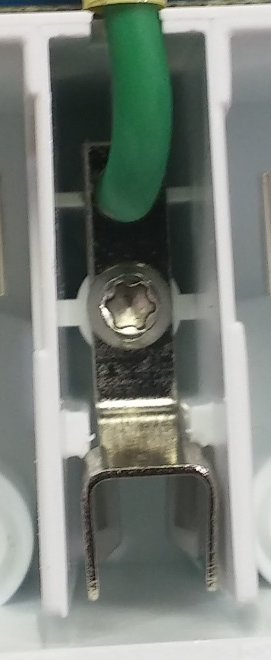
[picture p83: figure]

Good

Good

Bad

Bad

## AC power and ground tester

Put the cover on the power core, but don’t weld it yet
Attach a tester into one end of the extension cord and the other end to one of the power core receptacles. Repeat on the other receptacle.
Power up the power core, make sure the results from the testers read “CORRECT”
Make sure the plug retention is good, otherwise, send for rework to adjust brass placement

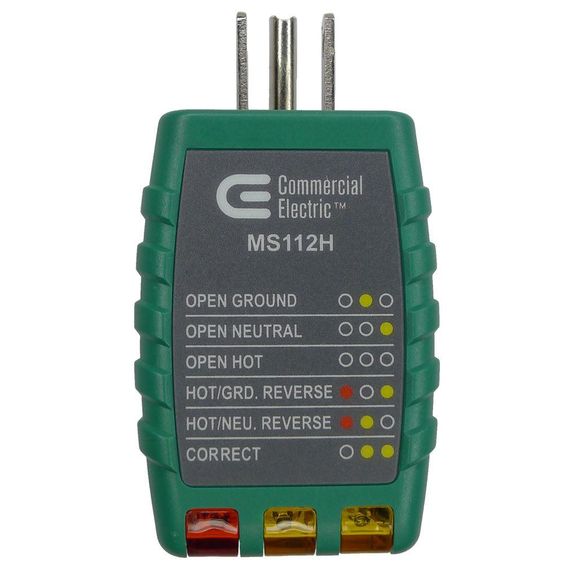
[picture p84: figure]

## 5V tester (Multimeter + modified test cables)

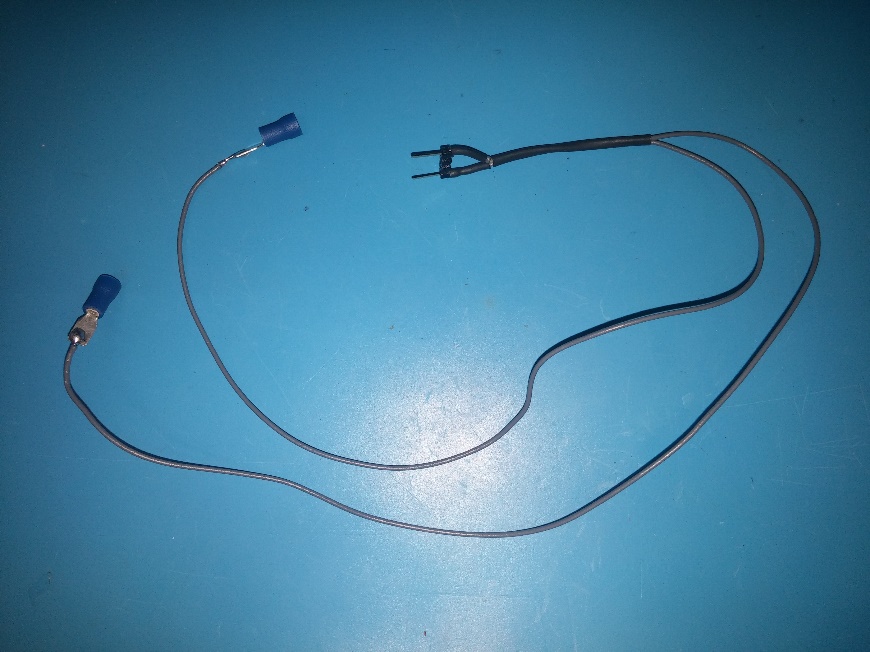
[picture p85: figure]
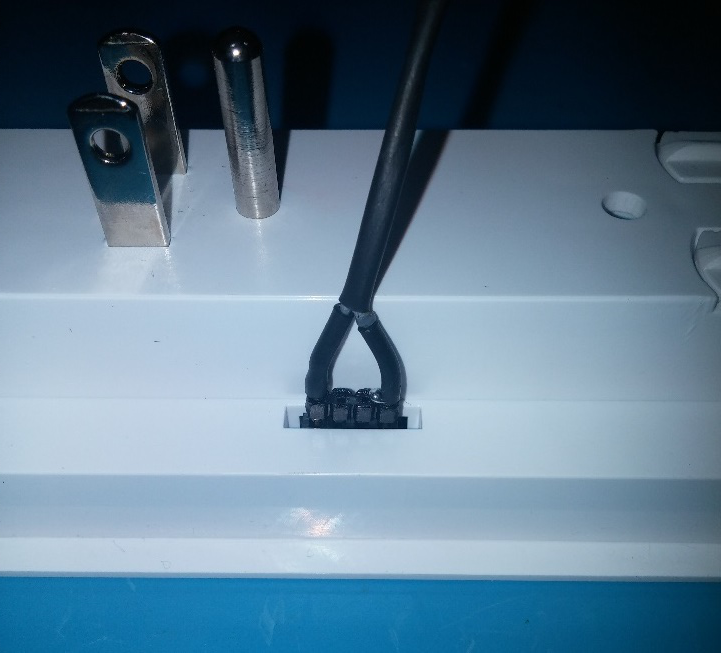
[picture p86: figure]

Build test cable
Insert test pins into one of the power core headers
Read ~5V with multimeter


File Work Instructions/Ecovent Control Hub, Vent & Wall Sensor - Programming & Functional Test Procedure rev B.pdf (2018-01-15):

Document No.: 202-00001
Revision: B

Ecovent® Control Hub, Vent & Wall Sensor – Programming & Functional Test Procedure

# Control Hub, Vent & Wall Sensor

# Programming & Functional Test Procedure

Ecovent® Control Hub, Vent & Wall Sensor – Programming & Functional Test Procedure

## Revision History

# | Revision | Description of Change | Created by: | Approved by: | DCR # | Release Date

1 | - | Initial Release | A. Smola | M. DeLorenzo | DCR-000003 | 01/13/2016
2 | A | Update based on Sanmina Feedback | A. Smola | A. Smola | DCR-000041 | 03/23/2016
3 | B | Expand vent functional test procedure | T. Frey

Ecovent® Control Hub, Vent & Wall Sensor – Programming & Functional Test Procedure

## Contents

Ecovent® Control Hub, Vent & Wall Sensor – Programming & Functional Test Procedure

## Device Programming

### Vent

The vent board is the simplest of the Ecovent boards, it has a single ST Micro STM32 Microcontroller. To program this device, select ‘Program Vent’ from the Ecovent Program + Functional Test application.

Figure 1

The user will be prompted to enter the serial number. This serial number is the vent PCBA serial number.


Figure 2

Ecovent® Control Hub, Vent & Wall Sensor – Programming & Functional Test Procedure

Scan the barcode (1D or 2D). It can be entered manually if necessary.

Figure 3

Place the vent PCB securely in the programming fixture. The programming fixture is shown below. Make sure that the power is plugged in and that the programming cable is attached. Make sure that the vent board is installed under the plexi-glass cover and that the cover is secured so that the board makes good contact. Place a weight on top of the plexi-glass cover to ensure good contact between board and programming fixture.


Figure 4

Once the user presses ‘OK’ the programming will begin. A progress bar will appear that will provide status.

Ecovent® Control Hub, Vent & Wall Sensor – Programming & Functional Test Procedure

Figure 5

When complete, a status will be presented indicating PASS or FAILURE.

PASS:


Figure 6

FAIL:

Figure 7

After the device is programmed the programming results and board serial number are uploaded to the Ecovent cloud. Additionally, a log file is produced. The log file is placed in the c:\users\ecovent\desktop\ecovent-functional-test\logs directory with a filename format “vent_<serial_number>.prog.log”

Ecovent® Control Hub, Vent & Wall Sensor – Programming & Functional Test Procedure

Figure 8

The log file contains output of the various programming steps in human readable output. If a failure occurs as part of programming, further details are available in log.


Figure 9

Ecovent® Control Hub, Vent & Wall Sensor – Programming & Functional Test Procedure

### Wall Sensor

The wall sensor board has an ST Micro MCU and a Bluetooth Module. When the wall sensor is programmed, both devices are automatically programmed. A failure of either device to program will result in a failure of the programming operation. To program the wall sensor, select 'Program Wall Sensor' from the menu.

Figure 10

The user will be prompted to enter the serial number. This serial number is the wall sensor top PCBA serial number.

Ecovent® Control Hub, Vent & Wall Sensor – Programming & Functional Test Procedure

Figure 11

Scan the barcode (1D or 2D). It can be entered manually if necessary.


Figure 12

At this point the user should secure the device in the programming fixture. The programming fixture is shown below. Make sure that the power is plugged in to the USB port (right side of picture) and that BOTH programming cables are attached. Make sure that the Wall Sensor board is installed under the plexi-glass cover and that the cover is secured so that the board makes good contact. The LED may turn yellow while the device is being programmed, this is OK.

Ecovent® Control Hub, Vent & Wall Sensor – Programming & Functional Test Procedure

Figure 13

Once the user presses ‘OK’ the programming will begin. A progress bar will appear that will provide status.


Figure 14

When complete, a status will be presented indicating PASS or FAILURE.

PASS:

Figure 15

FAIL:

Ecovent® Control Hub, Vent & Wall Sensor – Programming & Functional Test Procedure

Figure 16

After the device is programmed the programming results and board serial number are uploaded to the Ecovent cloud. Additionally, a log file is produced. The log file is placed in the c:\users\ecovent\desktop\ecovent-functional-test\logs directory with a filename format “ws_<serial_number>.prog.log”


Figure 17

The log file contains output of the various programming steps in human readable output. If a failure occurs as part of programming, further details are available in log.

Ecovent® Control Hub, Vent & Wall Sensor – Programming & Functional Test Procedure

Figure 18

Ecovent® Control Hub, Vent & Wall Sensor – Programming & Functional Test Procedure

### Control Hub

The control hub is the most complex of the Ecovent boards. Although the procedure is fully automated, there are several steps as part of the procedure. They are conducted in the order listed below.

There are three discrete programming steps:

1) Programming Operating System to NAND Flash
2) Installing Ecovent Application
3) Programming Microcontroller.

A fixture is provided for programming the hub. The board is installed in the fixture as shown below. The fixture is connected to the ST programmer via the blue connector. USB and Ethernet connections must be directly from the computer \ router to the Control Hub board.

Figure 19

To program the control hub, select ‘Program Hub’ from the menu.

Ecovent® Control Hub, Vent & Wall Sensor – Programming & Functional Test Procedure


Figure 20

The first prompt will be to enter the serial number. The serial number entered here is the control hub PCBA serial number. It should be scanned, but can be typed if necessary.

Figure 21

After entering the serial number, a dialog is presented with programming options. By default, all stages of programming are selected. If the board is being reworked due to a failed step, a subset of programming options can be selected.

Ecovent® Control Hub, Vent & Wall Sensor – Programming & Functional Test Procedure


Figure 22

Next, a dialog should popup indicating that a MAC address has been obtained. Ecovent has a Web based cloud service to manage its MAC addresses. The serial number of the device is sent to the cloud and the cloud provides a new MAC address or provides the previously assigned MAC address if it has already been assigned.

Figure 23

If the user is prompted for a MAC address that means that the programming software was unable to obtain a MAC address from the cloud.

The user will be prompted to Switch SW1 to OFF on the PCB, this should be the default position for the switch on a newly manufactured unit. Placing this switch in the OFF position allows the NAND flash to be programmed. In the ON position, the NAND flash cannot be programmed.

Ecovent® Control Hub, Vent & Wall Sensor – Programming & Functional Test Procedure

Figure 24


Figure 25

The user will then be prompted to attach USB programming cable. Make sure cable is inserted all the way. The board should power up.

Figure 26

Now, the user will be prompted to switch SW1 to ON position.

Ecovent® Control Hub, Vent & Wall Sensor – Programming & Functional Test Procedure


Figure 27

After pressing OK, a progress dialog will appear, this first phase should take approximately 5-10 seconds.

Figure 28

If the board is being programmed for the first time, after this completes, the board must be reset. The user will be presented with the following dialog prompting them to reset the board. Press reset, then press OK. If the board is being reprogrammed, do not reset the board at this step.

Figure 29

At this point, another progress dialog will be presented. This programming step takes much longer, approximately 3-5 minutes.

Ecovent® Control Hub, Vent & Wall Sensor – Programming & Functional Test Procedure


Figure 30

After completion of this step, the board must be reset again, the user will be prompted to do this.

Figure 31

When the board powers back on, the D11 LED should blink red for 2-3 seconds, then turn off, then turn solid ON. When it turns on solid press OK.

Figure 32

The D11 LED will remain solid red for approximately 3-5 minutes. It will then turn GREEN. When it turns GREEN, press OK.

Ecovent® Control Hub, Vent & Wall Sensor – Programming & Functional Test Procedure

Figure 33

Once the D11 LED turns GREEN, the first part of the programming process is complete.


Figure 34

At this point, the user should verify that the network cable is attached. A dialog will be presented…

The reset button should be pressed and the user should wait for the D11 LED to turn GREEN, then press OK. This will start the 2nd part of the programming process.

A progress box will be presented.


Figure 35

When this completes, the board has now had the application installed and a MAC address assigned. The third and last step is to program the MCU on the control hub.

If the board is in the fixture, the MCU programming leads are effectively attached. This step should only take approximately 30 seconds.

Ecovent® Control Hub, Vent & Wall Sensor – Programming & Functional Test Procedure

Figure 36

A progress bar will be presented and then either a success or failure dialog box will be shown.

Figure 37


Figure 38

If the programming steps were all successful, the device is now ready for functional test. If any of the steps failed, the device must be reprogrammed.

Ecovent® Control Hub, Vent & Wall Sensor – Programming & Functional Test Procedure

## Device Functional Test

### Vent

The Vent should be partially assembled as per the assembly instructions prior to functional test. Visually inspect vent to verify that the assembly was completed correctly. Refer to assembly visual aids and documentation.

a) Nuts are fully seated in doors: flat, and not creating any ‘wave’ shape
b) Doors are fully seated into the door track: no ribs are out of the track
c) Vent is assembled properly: Adequate clearance between door and outer box
d) All side screws installed and flush with the outer box
e) No excessive flash, scratches, dents, or contamination observed.

To test this device, select ‘Vent Functional Test' from the Ecovent Program + Functional Test application.

Figure 39

The device must be powered off the Ecovent provided networked power strip. Test code ensures that only one device is powered on at a time this way.

Verify that the Ecovent provided power adapter is plugged into white power cord associated with test station.

Ecovent® Control Hub, Vent & Wall Sensor – Programming & Functional Test Procedure

Figure 40

Then install battery pack adapter into vent.

Ecovent® Control Hub, Vent & Wall Sensor – Programming & Functional Test Procedure


Figure 41

The user will be prompted to enter the top level assembly serial number; this number should be scanned if possible but can be entered manually if necessary.

Subsequently the user will be prompted to enter the PCBA serial number; this number should be scanned if possible but can be entered manually if necessary.

The user must make sure that the KGU hub is powered on.

Ecovent® Control Hub, Vent & Wall Sensor – Programming & Functional Test Procedure

Figure 42

Figure 43

At this point, a database will be queried and if the vent PCBA has been programmed, if it has, the functional test will commence. If the device has not been programmed, an error message will be presented. If this error message is presented, the device should be reprogrammed. If after reprogramming functional test fails. The issue should be escalated to Engineering.


Figure 44

The functional test will start and a progress bar will be presented.

Ecovent® Control Hub, Vent & Wall Sensor – Programming & Functional Test Procedure

Figure 45

The vent will open and close once. Observe the motion of the doors to verify that the doors open and close fully. If visual confirmation of the cycle is missed, the process must be started from the beginning by power cycling the vent.

a) If the doors open and close fully, continue the test.
b) If the doors do not close fully, Mark as Failure
c) If the doors do not open fully, Mark as Failure

Examples of Passing Door Open & Close Conditions

Fully Opened Vent as shown from the Back (Note: All Vents, doors cannot be seen, hidden behind plastic outer box)

Ecovent® Control Hub, Vent & Wall Sensor – Programming & Functional Test Procedure

Fully Opened 10” Vent as shown from the Front (Note: Approximately 1 rib will be visible on 10 inch vents. 10” x 4” and 10” x 6” Only)

Fully Opened 12” Vent as shown from the Front (Note: No door parts will be visible on 12 inch vents. 12” x 4” and 12” x 6” Only)

Ecovent® Control Hub, Vent & Wall Sensor – Programming & Functional Test Procedure


Fully Closed Vent as shown from the Front (Note: All Vents, doors are completely closed and touching each other in the middle)

Ecovent® Control Hub, Vent & Wall Sensor – Programming & Functional Test Procedure

Examples of Failing Door Open & Close Conditions

Vent Not Fully Closed
(Note: Doors stop before touching each other, a gap can be seen)

Vent Not Fully Open
(Note: Doors stop before moving to a full open position)

Ecovent® Control Hub, Vent & Wall Sensor – Programming & Functional Test Procedure

When the functional test has completed, the user will be presented with a status indicating success or failure of the test. This indicator only applies to the communications portion of test, not the mechanical function portion. If vent does not open and close fully, vent should be scanned as a failure in the quality system.

Figure 46

On success, three labels will be printed. Two are identical product labels. These should be affixed to the vent as per the assembly instructions. If a label needs to be reprinted, please follow the instructions in the label printing section. The third is a label for the outside of the pulp packaging, it should be placed in the pulp packaging box and will be affixed later.

Figure 47

Ecovent® Control Hub, Vent & Wall Sensor – Programming & Functional Test Procedure

### Wall Sensor

The wall sensor should be fully assembled as per the assembly instructions prior to functional test. To test this device, select ‘Vent Functional Test' from the Ecovent Program + Functional Test application.


Figure 48

The user will be prompted to first enter the top level serial number; this number should be scanned if possible but can be entered manually if necessary. The user will then be prompted to enter the Sensor Ring PCBA serial number; this number should be scanned if possible but can be entered manually if necessary.

The wall sensor must be plugged into Ecovent provided networked power strip. It will power on automatically when needed by the test station software.

Ecovent® Control Hub, Vent & Wall Sensor – Programming & Functional Test Procedure

Figure 49

Figure 50

At this point, a database will be queried and if the device has been programmed, the functional test will commence. If the device has not been programmed, an error message will be presented:

Figure 51

If the device has been programmed, the functional test will start and a progress bar will be presented.

Ecovent® Control Hub, Vent & Wall Sensor – Programming & Functional Test Procedure

Figure 52

When the functional test has completed, the user will be presented with a status indicating success or failure of the test.

Figure 53

On success, two labels will be printed. The product label (FCC \ ETL) should be affixed to the wall sensor as per the assembly instructions. The pulp label should be attached to device with tape for subsequent application to pulp packaging. If a label needs to be reprinted, please follow the instructions in the label printing section.

Figure 54

Ecovent® Control Hub, Vent & Wall Sensor – Programming & Functional Test Procedure

Ecovent® Control Hub, Vent & Wall Sensor – Programming & Functional Test Procedure

### Control Hub

The hub can be fully assembled or partially assembled for functional test. Power must be applied to the hub and the hub must be connected via Ethernet to the router that the functional testing workstation is attached to. A KGU Wall Sensor with custom manufacturing image is required for the test.

The KGU Wall Sensor must be plugged into DUT extension cord that is connected to Ecovent networked PDU.

Select the hub functional test from the menu.


Figure 55

The operator will be prompted for serial number of board.

Ecovent® Control Hub, Vent & Wall Sensor – Programming & Functional Test Procedure

Figure 56

The cloud will be checked to verify that the serial number provided belongs to a board which has previously passes programming.

The control hub functional test requires the presence of a known good wall sensor to confirm proper operation of the radio.

When the control hub is powered up, after about 60 seconds it should blink blue.

After entering the serial number, the test will start.

A progress bar will be presented representing current state of test.


Figure 57

If the test passes, a dialog will be presented indicating such.

Figure 58

The KGU wall sensor should be reset at the end of the test.

Ecovent® Control Hub, Vent & Wall Sensor – Programming & Functional Test Procedure

## Label Printing

### Vent Device Label (FCC/ETL)

The label will automatically be printed at the end of the functional test, however, if a label needs to be re-printed, the user can select the 'Print Vent Label' option from the menu.

Figure 59

The user will be presented with a dialog box asking for the serial number. The serial number should be scanned if possible, but can be entered manually if necessary.

Figure 60

Ecovent® Control Hub, Vent & Wall Sensor – Programming & Functional Test Procedure

At this point, the database will be queried to confirm that the device serial number provided has been programmed and functionally tested prior. If not, the print request will fail.


Figure 61

Ecovent® Control Hub, Vent & Wall Sensor – Programming & Functional Test Procedure

### Wall Sensor Device Label (FCC/ETL)

The label will automatically be printed at the end of the functional test, however, if a label needs to be re-printed, the user can select the 'Print Wall Sensor Label' option from the menu.

Figure 62

The user will be presented with a dialog box asking for the serial number. The serial number should be scanned if possible, but can be entered manually if necessary.

Figure 63

Ecovent® Control Hub, Vent & Wall Sensor – Programming & Functional Test Procedure

At this point, the database will be queried to confirm that the device serial number provided has been programmed and functionally tested prior. If not, the print request will fail.

Figure 64

Ecovent® Control Hub, Vent & Wall Sensor – Programming & Functional Test Procedure

### Control Hub Device Label (FCC/ETL)

The label will automatically be printed at the end of the functional test, however, if a label needs to be re-printed, the user can select the 'Print Wall Sensor Label' option from the menu.


Figure 65

The user will be presented with a dialog box asking for the serial number. The serial number should be scanned if possible, but can be entered manually if necessary.

Figure 66

Ecovent® Control Hub, Vent & Wall Sensor – Programming & Functional Test Procedure

At this point, the database will be queried to confirm that the device serial number provided has been programmed and functionally tested prior. If not, the print request will fail.

Figure 67

Ecovent® Control Hub, Vent & Wall Sensor – Programming & Functional Test Procedure

### Pulp Packaging Label (All Devices)

The label will automatically be printed at the end of the functional test. If a label needs to be re-printed, the user can select the 'Print Wall Sensor Label' option from the menu.

Figure 68

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

Figure 69

At this point, the database will be queried to confirm that the device serial number provided has been programmed and functionally tested prior. If not, the print request will fail. The device type will determined based on the serial number and an appropriate pulp packaging label will be generated for the specific device.

Example Pulp Packaging Labels (device dependent)

Ecovent® Control Hub, Vent & Wall Sensor – Programming & Functional Test Procedure

Figure 70

Ecovent® Control Hub, Vent & Wall Sensor – Programming & Functional Test Procedure

## Appendix A - Troubleshooting

### Control Hub Programming Fails

- USB Programming Cable is Not Attached
- ST Link Programmer Is Not Connected
- Network Cable Is Not Connected
- Serial Number is Invalid
- Cloud Service Cannot Be Reached to Fetch MAC Address
- COM Port Configuration for USB Programming Cable Is Not Correct

### Vent or Wall Sensor Programming Fails

- Serial number is invalid.
- Board does not have power.
- Board is not secure in programming fixture.
- Programming \ power cable(s) are not properly connected between programming fixture and computer.
- PCBA is bad.
- Wrong device was selected when programming.

### Vent or Wall Sensor Functional Test Fails

- Serial number is invalid.
- Device was not programmed prior to testing.
- All sensors are not attached to PCBA.
- Wall sensor or vent was not reset prior to start of test.
- There is a problem with KGU HUB
- Wrong device was selected when performing functional test.

### Label Printing Fails

- Device was not programmed.
- Device was not tested.
- Serial number is invalid.
- Printer is 'OFFLINE' instead of 'ONLINE'
- Printer connection problem.

Ecovent® Control Hub, Vent & Wall Sensor – Programming & Functional Test Procedure

## Appendix B – Network Topology


Ecovent® Control Hub, Vent & Wall Sensor – Programming & Functional Test Procedure

## Appendix C – Simultaneous Test \ Program Matrix

Effective March 15, 2016

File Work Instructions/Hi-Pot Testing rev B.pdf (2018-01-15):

### Ecovent Wall Sensor “HiPot” (Dielectric Voltage Withstand Test)

1. 100% of Wall Sensors 901-00010 must be tested compliant to the ETL test specification provided.
2. Test must be performed at the final assembly level at a minimum of 1500 VAC for 1.00 seconds.
3. Test records must be retained by testing organization with certificate of compliance for every production lot.
4. See production floor work instructions below for detailed test procedure and visual aids.

### 11.0 Manufacturing and Production Tests

The manufacturer agrees to conduct the following Manufacturing and Production Tests as specified:

Required Tests
Dielectric Voltage Withstand Test

### 11.1 Dielectric Voltage Withstand Test

Method
One hundred percent of production of the products covered by this Report shall be subjected to a routine production line dielectric withstand test.

The test shall be conducted on products, which are fully assembled. Prior to applying the test potential, all switches, contactors, relays, etc., should be closed so that all primary circuits are energized by the test potential. If all primary circuits cannot be tested at one time, then separate applications of the test potential shall be made.

The test voltage specified below shall be applied between primary circuits and accessible dead-metal parts. The test voltage may be gradually increased to the specified value but must be maintained at the specified value for one second or one minute as required.

Test Equipment
The test equipment shall incorporate a transformer with an essentially sinusoidal output, a means to indicate the applied test potential, and an audible and/or visual indicator of dielectric breakdown.
The test equipment shall incorporate a voltmeter in the output circuit to indicate directly the applied test potential if the rated output of the test equipment is less than 500VA.
If the rated output of the test equipment is 500VA or more, the applied test potential may be indicated by either:
1 - a voltmeter in the primary circuit;
2 - a selector switch marked to indicate the test potential; or
3 - a marking in a readily visible location to indicate the test potential for test equipment having a single test potential output.
In cases 2 and 3, the test equipment shall include a lamp or other visual means to indicate that the test potential is present at the test equipment output. All test equipment shall be maintained in current calibration.

Products Requiring Dielectric Voltage Withstand Test:
Product | Test Voltage | Test Time
All products covered by this Report. | 1240V | 60 s
| or
| 1488V | 1 s
Revision | Author | Date
A | Pentecost | 2.16.16
B | Pentecost | 2.23.16

### Ecovent HiPot Test Procedure For Wall Sensor 901-00010

Description: | Instructions for setting up and performing the HiPot test on the Ecovent Wall Sensor assembly. 100% of devices must be tested with results recorded by serial number in SFDC.
Equipment Required: | 1. Associated Research Quadchek Model 6554SA HiPot Tester or equivalent.
2. Ecovent HiPot Cable (see Figure 1)


Figure 1. Ecovent HiPot Cable Connected to Wall Sensor

Reference Documents: | 1. Associated Research Model 6554SA Operation and Service Manual
2. Attachment A - Settings For Quadchek 6554SA HiPot Tester

NOTE: Prior to performing the HiPot test, verify that the “Quadcheck Ground Continuity/Hi-Pot Verification Test” (SOP-4-1041-340) was performed that day and that the HiPot/Ground Bond “Just Fail” Log (SOP-4-1035-340) was filled out with the test record. If there is no entry on the “Just Fail” log for today’s date, stop and contact engineering.

To Recall and Enter/Edit a Program (See Appendix A for HiPot instrument settings):
(Refer to Figure 2)
1. Press ‘RECALL’ key.
2. Type desired program number ‘xx’ using numeric keypad (Enter 15 for Ecovent Wall Sensor HiPot).
3. Press ‘ENTER’ key. Skip to “Performing the HiPot Test” if you are not entering a new program or changing an existing one.
4. Press ‘REVIEW’ key.
5. Press down arrow or up arrow keys to scroll through menus.
6. Use the ‘DATA ENTRY’ and ‘ENTER’ keys to change or toggle between selections.
7. Press ‘RUN/CLEAR’ key.
8. Press ‘STORAGE’ key
9. Select a memory to store the program in (1-15).
NOTE: The Ecovent program is stored in location 15.
10. Press ‘ENTER’ key.


Figure 2. Quadchek Data Entry Keypad and Display

Performing the HiPot Test:

1. Connect the Ecovent HiPot cable as shown in Figures 1 & 3.


Figure 3. Ecovent Wall Sensor HiPot Cable Connections to Quadchek.

2. Press ‘TEST’ key on HiPot tester. See Figure 2.
3. Wait approximately 30 seconds.
4. If ‘PASS’ status indicator illuminates (green), then the test passes. Perform the following:
a. Disconnect the HiPot Cables from the UUT.
b. Scan the Ecovent Wall Sensors serial number into SFDC as a “PASS” and initial/date the traveler. Move the Wall Sensor to the next step in the process.
5. If the ‘FAIL’ status indicator illuminates then test fails. Scan the serial number of the board into SFDC as a fail and move it into the Debug area.

Appendix A – Settings For Quadchek 6554SA HiPot Tester

This is what should be loaded into the program 15 location on the Quadchek: (Another program number could also be used if it is available)

R = | OFF
CON = | OFF
G = | OFF
W = | ON
WVS = | 1500
WHA = | 10.0
WLA = | 0.0
WTS = | 1
WRT = | 30
WMD = | AC
WHZ = | 60Hz
ARC = | ON
WCH = | 00000000

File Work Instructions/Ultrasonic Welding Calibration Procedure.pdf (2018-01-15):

## Ecovent Systems

## Power Core Ultrasonic Welding

## Work Instruction

Power Button; Air Line; Booster Faceplate; Horn Tool; Tools for Machine Adjustment; Anvil Fixture; Leveling Plate; Finger Buttons; Emergency Stop Button

Revision Control:

Author | Revision | Date
Pentecost | Initial Release | 1.30.16

Equipment Setup
1. Locate and use ear and eye protection. If you cannot find the appropriate equipment, stop and contact engineering. Notify nearby coworkers who may also want to utilize ear protection.
2. Check electrical cables and pneumatic hoses are securely connected. If any connections are damaged or unsafe, stop and contact engineering.


3. Power on the Ultrasonic Welder on the left of the machine as shown.
4. Verify that the Welder powered up correctly with no error codes shown. The digital display should read “ready”. If it does not, stop and contact engineering.


5. Verify that the correct fixture is installed: 109-156-6316 // ATG 504 // BUC 942999
6. Verify that the correct horn tooling is installed: 109-163-2461 // ATG 505 // BUC 942999


7. Verify that the horn tooling is retracted fully upward in the ‘home’ position.


8. Verify that the horn is properly aligned to the fixture.
a. Place an empty sample workpiece into the lower fixture as shown.
b. Press the “Horn Down” button. The screen will update to 0.0000”. If it does not, stop and contact engineering.


c. Actuate the weld head by simultaneously pressing the buttons on the sides of the machine.


Sample piece is in the
anvil fixture

Simultaneously press
the buttons on the
sides to actuate the
weld head

Horn is retracted in the
home position d. The weld head will move down to contact the workpiece.
e. The digital display will update with a reading of the travel distance – it should be between 2 and 3 inches. Record this value in the provided setup sheet. If this value deviates from the previous 10 recorded values by more than +/- 0.1000”, stop and contact engineering.


f. Inspect the top tool for orientation with respect to the workpiece. The tool should be aligned to the workpiece such that the powercore faceplate is fully covered by the tool face. If the tool is rotated or skewed, or if the faceplate is not uniformly covered by the weld tool, stop and contact engineering.

Travel Distance read
should be between
2.000” and 3.000”.

Record the value in the
log sheet under “travel
distance”


Horn face completely
covers the faceplate.
This alignment is good!

g. If the orientation of the weld tool is good, continue with the equipment setup. Return the weld head to “home” position by pressing the “Horn Down” button again.


9. Verify the ultrasonic power dissipated in air by the stack. Make sure you have your ear protection in use – a high frequency ultrasonic sound will be heard. Press the ‘Test’ button and hold for 4-6 seconds until a value is shown on the screen. Record the value on the log sheet. If the value recorded deviates from the previous 10 records by more than +/- 2.0 , stop and contact engineering .


10. Prepare the machine to check leveling.
a. Adjust the machine parameters for the leveling test (parameters listed below).
b. To adjust the input pressure: Pull the knob (toward you) to unlock the knob and allow adjustment. Turn clockwise to increase the pressure. Turn counterclockwise to decrease the pressure. Turning the knob counterclockwise might not yield a decrease in the pressure gauge reading due to remaining pressure in the cylinder. To release the remaining pressure, press the “horn down” button and actuate the finger buttons. The pressure gauge reading will stabilize again to the current system pressure, and the setpoint adjustment can be made. Once the desired setpoint is reached, press the knob

Record this value in the
setup sheet under
“Ultrasonic Power
Test”

away from you (towards the machine) to lock the pressure setpoint. If the desired pressure setpoint cannot be met, stop and contact engineering.


c. To adjust the welding parameters, use the arrow keys as shown. The up arrows will increase the setpoint, while the down arrows will decrease the setpoint. Use the double arrow buttons for coarse adjustment (large changes) to the setpoint and use the single arrow buttons for fine adjustment (small changes) to the setpoint

### Powercore Ultrasonic Welding LEVELING SETUP Settings

Input Pressure | 50 +/- 2 psig
Trigger Force | 4
Weld Time | .100 sec
Hold Time | .500 sec

Pull this knob towards you to adjust the pressure.
Turn clockwise to increase the pressure. Turn
counter clockwise to
decrease the pressure.
Record the final setpoint
value in the setup sheet
under “Input pressure”
(psi)


Use these arrows to adjust the welding parameters
for weld time and hold
time.

d. Locate carbon paper and a blank sheet of white paper.
e. Locate a sample work piece and place it in the lower fixture as shown. First, load the housing. Note the orientation of the housing with respect to the cutout in the fixture. The part must always be loaded such that the prong locations are on the right side as shown. Next, load the faceplate onto the powercore.
f. Place the white sheet of paper on top of the workpiece.
g. Place the carbon paper on top of the white sheet of paper.


Carbon Paper Setup | Good Leveling | Bad Leveling
h. Execute a weld by simultaneously pressing the buttons on either side of the machine.
i. Remove the carbon paper and inspect the white sheet for an imprint of the part. Compare the imprint to the visual aids above. The imprint of the faceplate cover should be uniform around the entire perimeter of the part, indicating that there is even pressure across the entire face. If there are any voids or areas of low or light coloration, this indicates bad leveling setup. If the imprint is good, record leveling record in the provided log sheet by writing “OK” in the column labeled “Leveling Test Record” and continue with the setup process. If the imprint is bad, stop and contact engineering.
j. Retain the imprint of the carbon paper and white sheet. Staple the carbon paper to the white sheet and label the white sheet with the production lot number, date, time, and operator’s initials. Provide this record to engineering for storage and quality purposes.
11. Return the welder to the desired production settings using the instructions above.
12. Record the production settings used in the appropriate columns in the setup sheet.

### Powercore Ultrasonic Welding PRODUCTION Settings

Input Pressure | 30.0 +/- 2.0 psig
Trigger Force | 4
Weld Time | .180 sec
Hold Time | .300 sec
13. Locate a sample workpiece from the supplied components bin designated “Use for Setup”

14. Load the part into the fixture. First, load the housing. Note the orientation of the housing with respect to the cutout in the fixture. The part must always be loaded such that the prong locations are on the right side as shown.
15. Simultaneously press the buttons on either side of the machine to perform one weld using the setup piece.
16. Record the “Actual” collapse measured by the machine in the setup sheet. To determine this value, press the “Actual” button on the machine face two times until a reading in inches is shown. The value must be between .018” and .025” . If it is outside of these limits, stop and contact engineering.


17. Remove the part from the fixture and inspect.


a. Faceplate must be securely seated to the housing with no warpage or bowing observed. Apply force to attempt to remove the faceplate cover from the housing. No movement or cracking should be felt or observed.
b. Inspect the weld seam. No flash should be protruding from the weld joint. The appearance of the weld seam should be uniform around the entire perimeter of the assembly. See provided visual aids. If the appearance of the weld seam is acceptable, write “OK” in the column on the setup sheet labeled “Setup Part – Visual Inspection”. If the appearance of the weld seam is unacceptable, stop and contact engineering.
c. Measure the weld seam gap using feeler gages. Use the provided feeler gages to determine the weld gap between the housing and the faceplate. Start with a .010” thick gage and insert it between the housing and the faceplate cover around the entire perimeter of the device.
i. If the gage can fit into the gap, try the next size larger gage until it can no longer consistently fit into the gap around the entire perimeter of the device.
ii. If the first .010” gage used cannot fit into the gap, try the next smallest size, until the gage can consistently fit into the gap around the entire perimeter of the device.

iii. Record the largest size gage that can fit into the gap on the setup sheet under the column “Feeler Gage Measurement”


18. Verify that the setup sheet record in the provided log sheet is complete, with no entries missing or outside of the control limits. If any entries are missing or outside of the control limits, stop and contact engineering. Sign your initials as the responsible person for this setup record and continue with the production lot.

Feeler gage measures the
gap between the housing
and the faceplate cover

Record the largest size
feeler gage that can fit in this gap

Power Core Welding Production Process
1. Verify Setup Procedure was followed and the setup record is recorded in the log sheet provided.
2. Setup procedure must be performed and recorded in the setup sheet at the following intervals:
a. At the beginning of each shift
b. Every 4 hours
c. After machine maintenance
d. After downtime exceeding one hour
e. After any engineering testing
f. At any additional intervals at the discretion of Sanmina or Ecovent engineering
3. Retain all setup parts in a labeled plastic bag with the production lot number and date for identification. Setup parts and carbon paper/white sheet leveling records must be retained for one year from date of manufacture.
4. On a weekly basis, transfer the setup records in the setup sheet to digital record and submit to Ecovent engineering for review. Statistical process control will be used to monitor weld collapse over time.
5. Powercores must be 100% tested for 5V Power and GND Test. See appropriate work instruction for detailed procedure
6. Powercores must be sample basis tested for 1500VAC HiPot in accordance with the ANSI statistical sampling guideline below based on the powercore lot size:


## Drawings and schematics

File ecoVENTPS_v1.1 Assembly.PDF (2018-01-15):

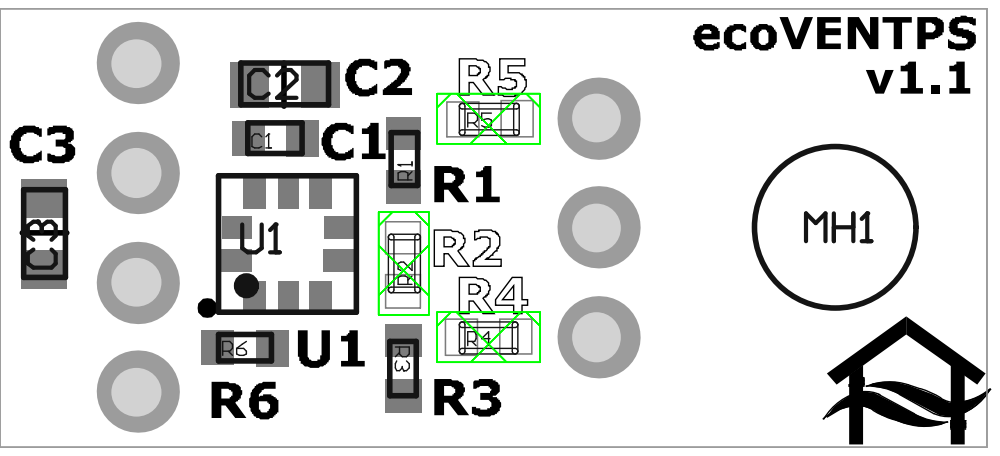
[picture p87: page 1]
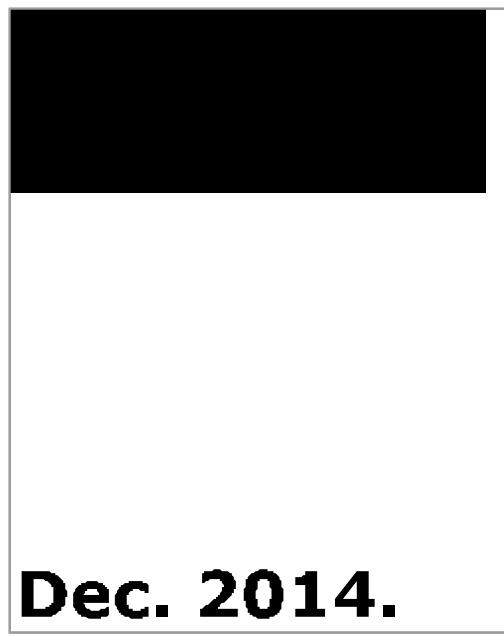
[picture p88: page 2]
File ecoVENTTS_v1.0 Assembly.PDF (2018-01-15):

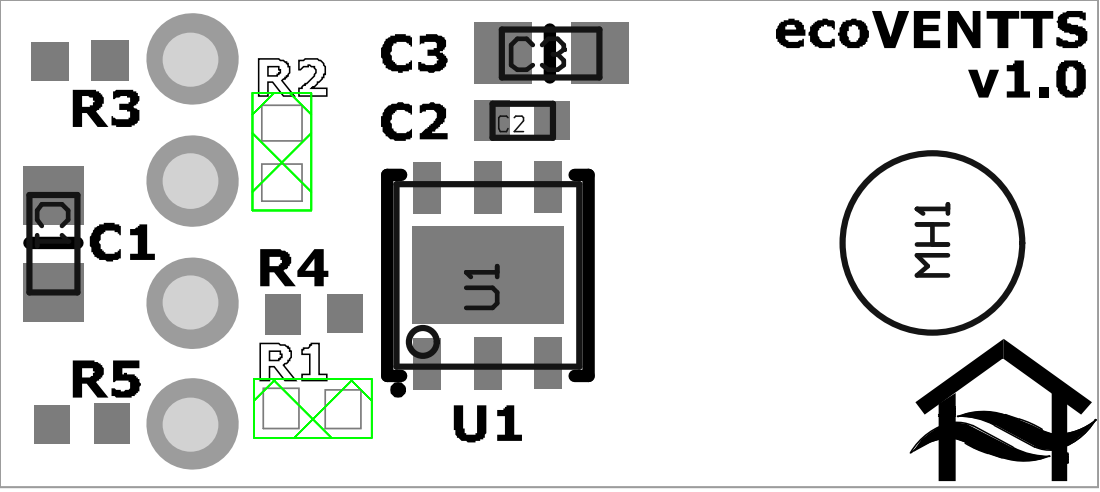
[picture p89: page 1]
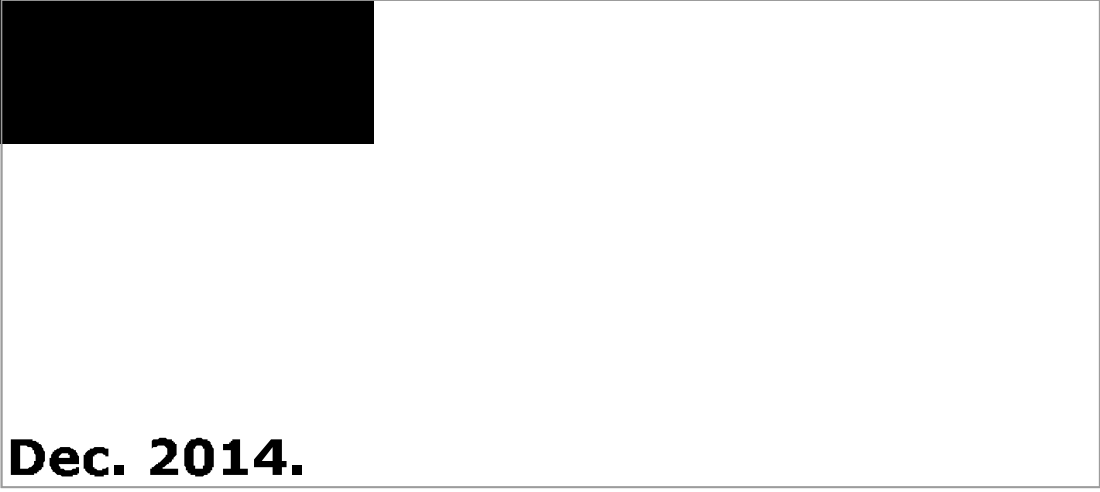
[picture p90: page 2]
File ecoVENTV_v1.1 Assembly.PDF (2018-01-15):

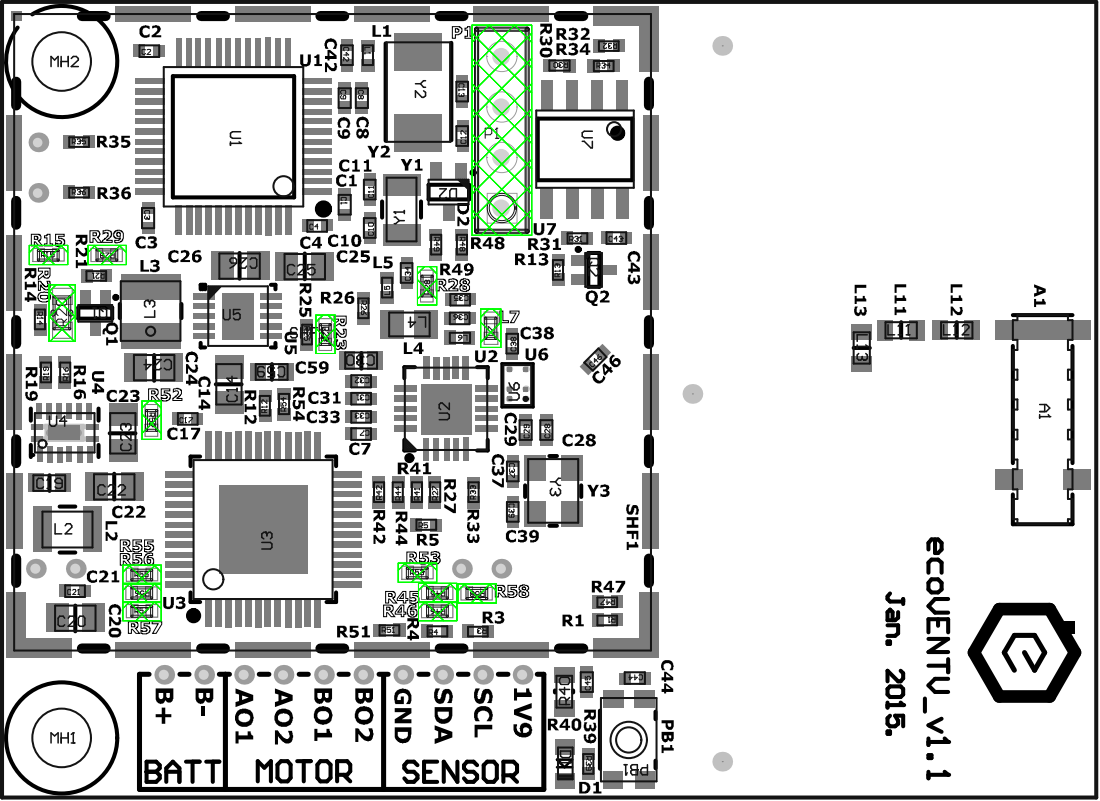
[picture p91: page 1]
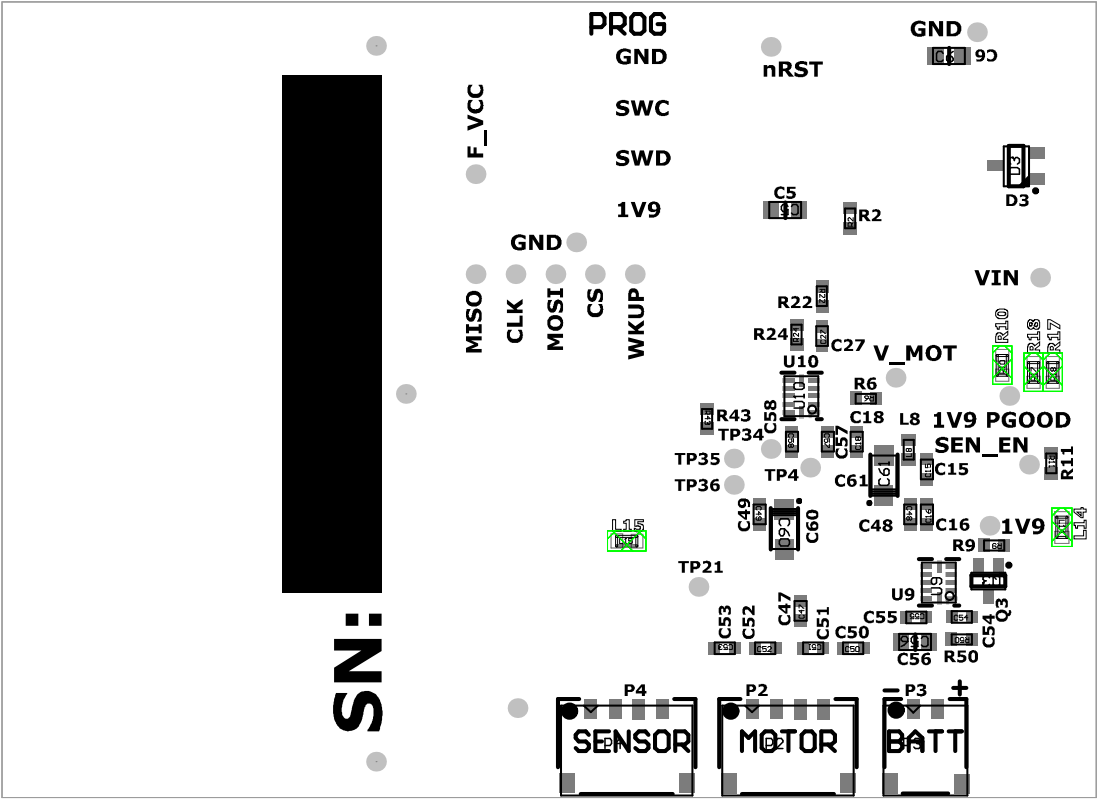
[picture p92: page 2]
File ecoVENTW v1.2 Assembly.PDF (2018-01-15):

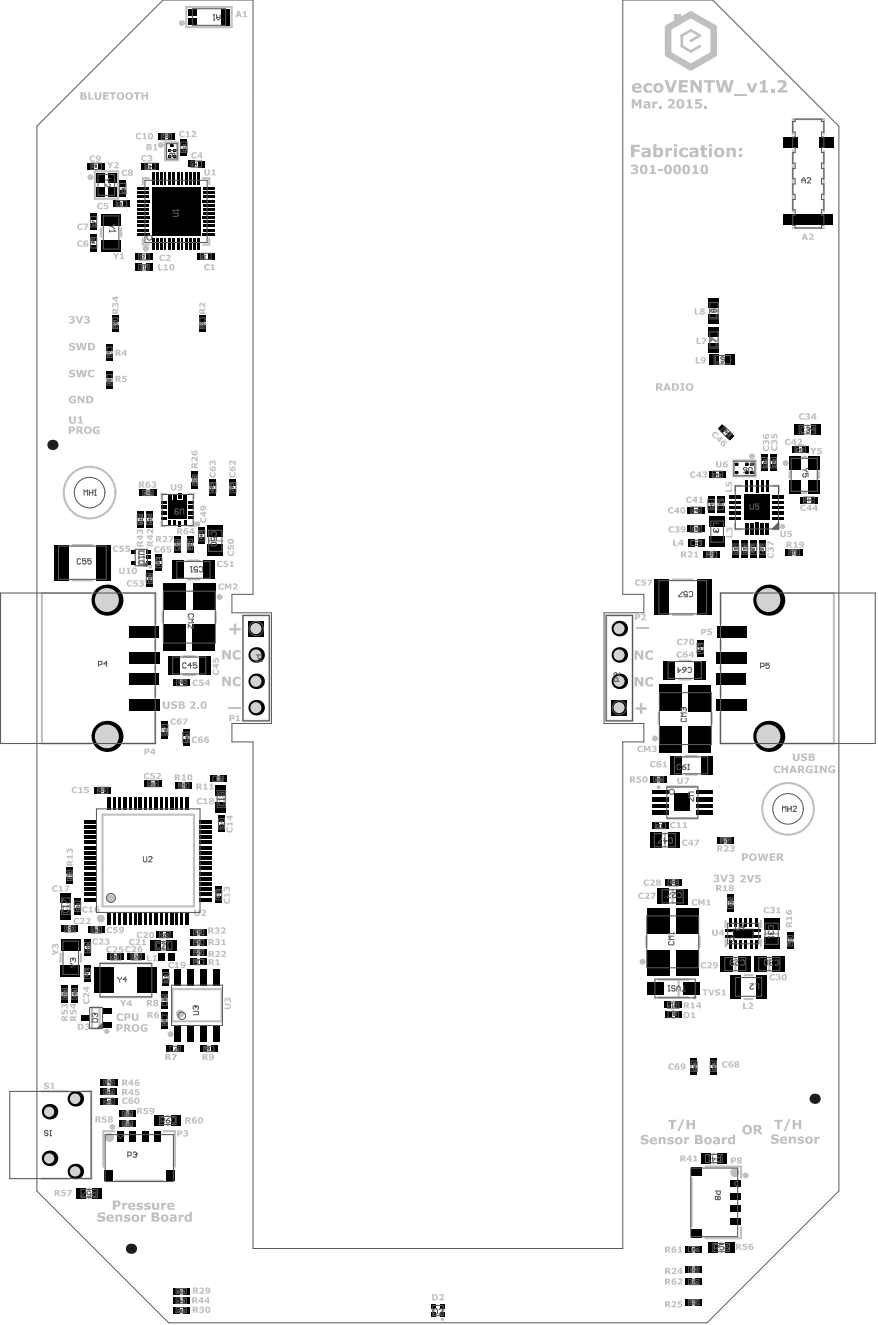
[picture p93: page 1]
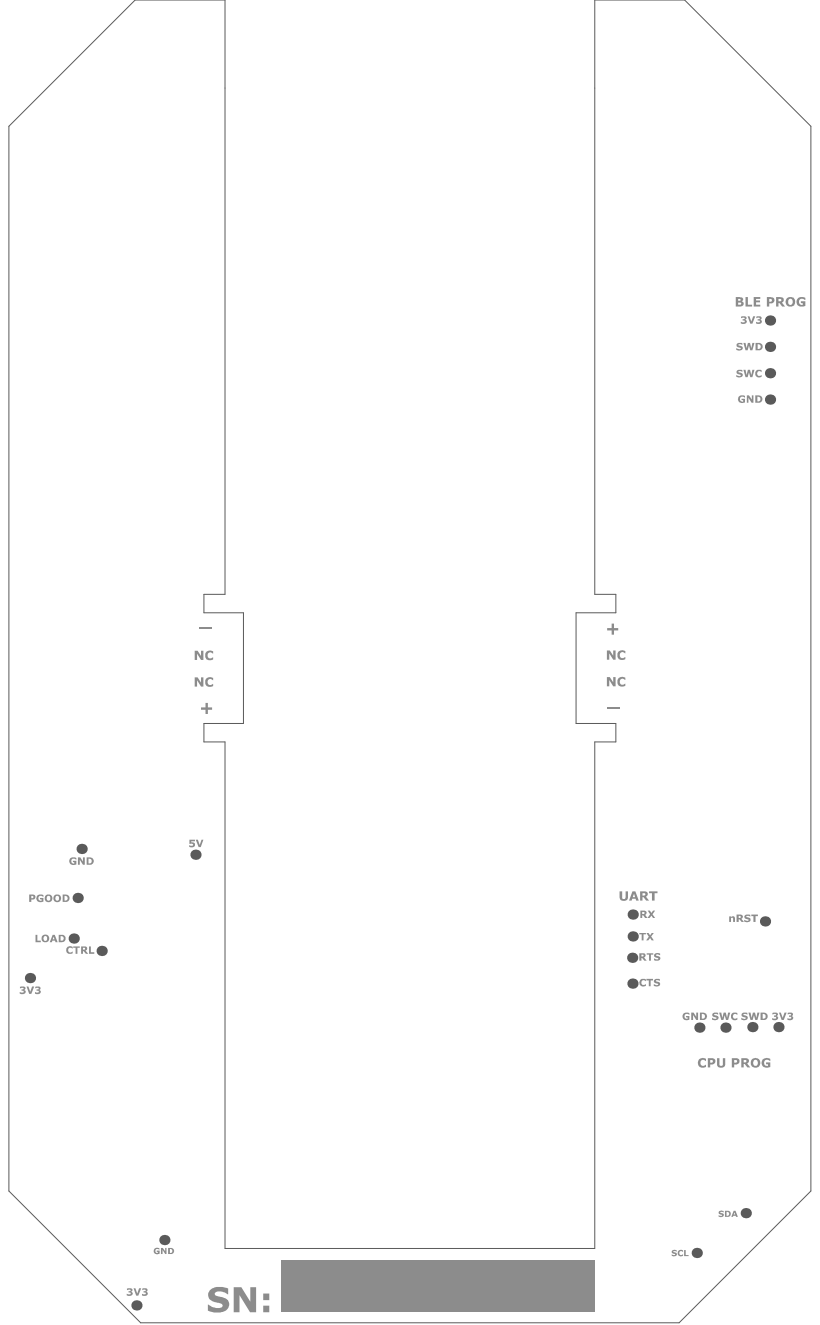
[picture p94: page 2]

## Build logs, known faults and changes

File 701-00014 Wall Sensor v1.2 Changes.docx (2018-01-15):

701-00014 Wall Sensor v1.2 Changes

101-00058 | 2 more added (CM2, CM3 ), qty. is now 3
301-00010 | Added to replace v1.1 PCB
101-00005 | Remove C48, change qty. from 21 to 20
101-00020 | Added 8 Caps/Ref.Des. qty. is now 9
